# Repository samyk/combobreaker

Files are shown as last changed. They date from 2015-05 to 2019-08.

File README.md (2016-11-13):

# [C-C-C-C-Combo Breaker](http://samy.pl/combobreaker/)

**[Combo Breaker](http://samy.pl/combobreaker/)** is a motorized, battery powered, 3D printed, Arduino-based combination lock cracking device. It is portable, open source, 3D models provided, and exploits a new technique I've discovered for [cracking combination locks in 8 attempts or less](https://www.youtube.com/watch?v=09UgmwtL12c), but in an even more exciting, automated fashion.

By [@SamyKamkar](https://twitter.com/samykamkar)

#### Follow me on [Twitter](https://twitter.com/samykamkar) or [join my mailing list](http://samy.pl/list/) to hear about future projects and research.

**Live demonstration** and full details available in [the video](https://www.youtube.com/watch?v=YcpSvHpbHQ4):
<a href="https://www.youtube.com/watch?v=YcpSvHpbHQ4" target="_blank">KeySweeper</a>

-----

**Point of Contact:** [@SamyKamkar](https://twitter.com/samykamkar) // <http://samy.pl>

**Video demonstration / explanation:** [https://youtu.be/YcpSvHpbHQ4](https://youtu.be/YcpSvHpbHQ4)

**Released:** May 14, 2015

**Source code / 3D models:** [https://github.com/samyk/combobreaker](https://github.com/samyk/combobreaker)

**Unit Cost:** < $100

**Status:** Operational, open source, open hardware, declassified.

-----

# (U) Hardware

Combo Breaker (http://samy.pl/combobreaker/sIMG_2916.JPG)

### [Arduino Nano](http://amzn.to/1QLlf23)
**$12**: A [5V Arduino Nano](http://amzn.to/1QLlf23) microcontroller is used as the brains of the project.

### [Allegro A3967 / EasyDriver Stepper Driver](http://amzn.to/1A1Ovxl)
**$20**: I originally used an A3967-based [EasyDriver](http://amzn.to/1A1Ovxl) which can drive a stepper motor up to 30V at 750mA. This is what precisely controls the dial.

### or [Allegro A4988](http://amzn.to/1L3q7fK)
**$7**: Instead of the EasyDriver, I upgraded to a smaller, yet more powerful stepper driver that can go up to 1 amp (1000mA).

### [Stepper Motor](http://amzn.to/1FfLUQG)
**$30**: You can use a normal stepper motor for the "simpler" version of the Combo Breaker build, however if you're working on creating the more advanced version, you'll need a double-shaft stepper motor like I liste below.

### or [Double Shaft Stepper Motor](http://www.phidgets.com/products.php?product_id=3320)
**$16**: This double shaft stepper motor allows you to build the more advanced Combo Breaker while employing an optical rotary encoder on the back to detect the position of the stepper when the dial stops turning (which is part of the exploit employed).

### [HKT22 Optical Rotary Encoder](http://www.phidgets.com/products.php?product_id=3531)
**$25**: For use **only** with the double shaft stepper motor, this optical rotary encoder lets us know what position the shaft of the stepper motor is at and allows us to employ an exploit on Master combination locks where the stepper will get locked into certain grooves within the internal combination disc of the lock.

### [Analog Feedback Servo](https://www.adafruit.com/products/1404)
**$15**: This servo not only provides the torque we need to lift the shackle (90.26 oz*in), but has an additional wire providing analog feedback that we use to detect the state of the shackle and whether it has opened or not.

### [L7805 Voltage Regulators](http://amzn.to/1A28XOt)
**$6**: If you're using the analog feedback servo, you'll want to use an external voltage regulator to provide enough juice to the servo. While the Arduino is 5V and can drive the servo normally, it won't be able to pump out enough current for the servo when it starts hitting the shackle and could damage your Arduino.

### [500mAh 3S Lipo Battery](http://amzn.to/1PkRVlz)
**$20**: This 500mAh 3S (3-cell, 11.1V) battery gives enough juice to the stepper motor to be very effective, and at 500mAh can last between 30-120minutes straight before having to be recharged.

### [Lipo Charger](http://amzn.to/1A1Q2n7)
**$50**: This lipo charger is overkill if only used for this project, but is a good one that I use at home for a wide range of batteries and cells. You don't need this one, but if you want to recharge the battery, you'll need a charger that supports 3-cell LiPos.

### [Arctic Alumina Thermal Adehsive](http://amzn.to/1PkTakG)
**$8**: Not required, but this is the thermal **adhesive** I use to **permanently** attach the heatsink to the stepper motor driver. Normal thermal paste has very little adhesion and kept falling off, so I switched from thermal paste to this thermal adhesive.

### [Digital Calipers](http://amzn.to/1K8juex)
**$16**: If you don't already have digital calipers for precise measurements to measure the lock, for example, these are inexpensive and accurate.

### [Breadboard and Wires](http://amzn.to/1FfMb6e)
**$6**: If you don't already have a breadboard and wires, they will kind of help.

Combo Breaker (http://samy.pl/combobreaker/sIMG_2875.JPG)

Combo Breaker (http://samy.pl/combobreaker/sIMG_2920.JPG)

-----

# (U) Software

### Combo Breaker
Combo Breaker's source code can be obtained in entirety from my github: <https://github.com/samyk/combobreaker>

Combo Breaker 3D Print (http://samy.pl/combobreaker/model.jpg)

-----

# (U) 3D Models

I've included the 3D models on my github: <https://github.com/samyk/combobreaker>
 
Combo Breaker 3D Print (http://samy.pl/combobreaker/smodel.png)

Combo Breaker (http://samy.pl/combobreaker/sIMG_2919.JPG)

-----

# (U) Contact

**Point of Contact:** [@SamyKamkar](https://twitter.com/samykamkar)

You can see more of my projects at <http://samy.pl>.

#### Follow me on [Twitter](https://twitter.com/samykamkar) or [join my mailing list](http://samy.pl/list/) to hear about future projects and research.

Thanks!

------

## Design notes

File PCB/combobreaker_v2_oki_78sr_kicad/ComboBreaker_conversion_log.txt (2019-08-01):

#********** START OF renumber-sheet.ulp ULP Version 4.4.4 12-03-2017 :20:05:27 LOG **********#
#OldRef				SheetNumber	NewRef
ARDUINO				1	ARDUINO4989
ENCODER				1	ENCODER4989
OKI-78SR				1	OKI-78SR4989
SERVO				1	SERVO4989
STEPPER				1	STEPPER4989
#********** END OF renumber-sheet.ulp ULP Version 4.4.4 12-03-2017 :20:05:27 LOG **********#

#********** START OF fix_via_hack.ulp ULP Version 4.6.0 12-03-2017 :20:05:32 LOG **********#
PADFILL	PadCount=60		Net=GND				(X=8145.000000 Y=34052.000000)	LayerStart=1	LayerEnd=1
#********** END OF fix_via_hack.ulp ULP Version 4.6.0 12-03-2017 :20:05:32 LOG **********#

#********** START OF eagle6xx-sch-to-kicad-sch.ulp 1.9 12-03-2017 :20:06:57 LOG **********#
    Conversion completed with no Messages
#********** END OF eagle6xx-sch-to-kicad-sch.ulp 1.9 12-03-2017 :20:06:57 LOG **********#

#********** START OF exp-lbrs.ulp 6.6 12-03-2017 :20:11:32 LOG **********#
OK: Eagle lib export from SCH/PCB OK
    Conversion completed with no Messages
#********** END OF exp-lbrs.ulp 6.6 12-03-2017 :20:11:32 LOG **********#

#********** START OF eagle-lbr2kicad-1.0.ulp 2.7 12-03-2017 :20:11:44 LOG **********#
Missing Prefix Part =''				A4988BREAKOUT					ComboBreaker		M
Missing Prefix Part =''				OKI-78SRH					ComboBreaker		M
#********** END OF eagle-lbr2kicad-1.0.ulp 2.7 12-03-2017 :20:11:44 LOG **********#

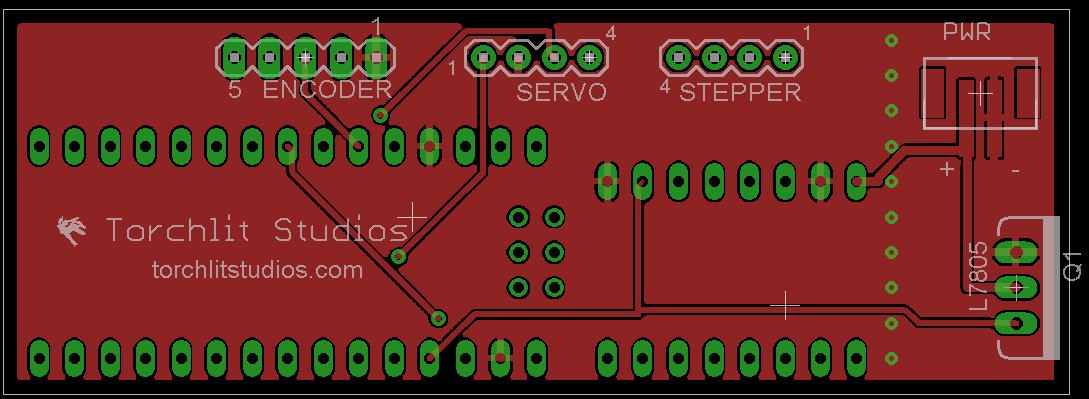
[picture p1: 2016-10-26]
Eagle Files/ComboBreaker_top.png

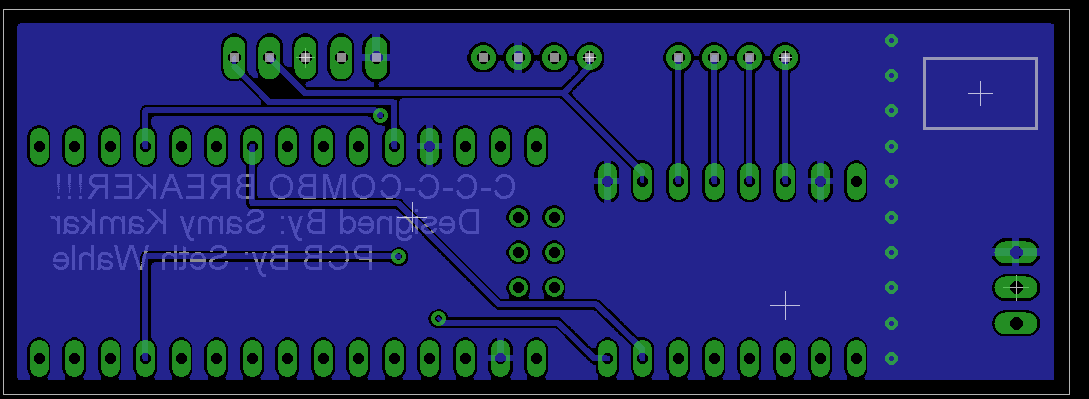
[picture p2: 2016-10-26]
Eagle Files/ComboBreaker_bottom.png

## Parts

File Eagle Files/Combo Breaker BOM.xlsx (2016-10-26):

JST-PH-2-SMT | https://www.sparkfun.com/products/8612
L7805CV | http://www.mouser.com/ProductDetail/STMicroelectronics/L7805CV/?qs=9NrABl3fj%2FqplZAHiYUxWg%3D%3D
STEP-STICK | http://www.ebay.com/itm/like/281574528914?lpid=82&chn=ps
Arduino Nano | http://www.newegg.com/Product/Product.aspx?Item=9SIA7BF2K19102&nm_mc=KNC-GoogleMKP-PC&gclsrc=aw.ds
Pin Headers | https://www.sparkfun.com/products/116

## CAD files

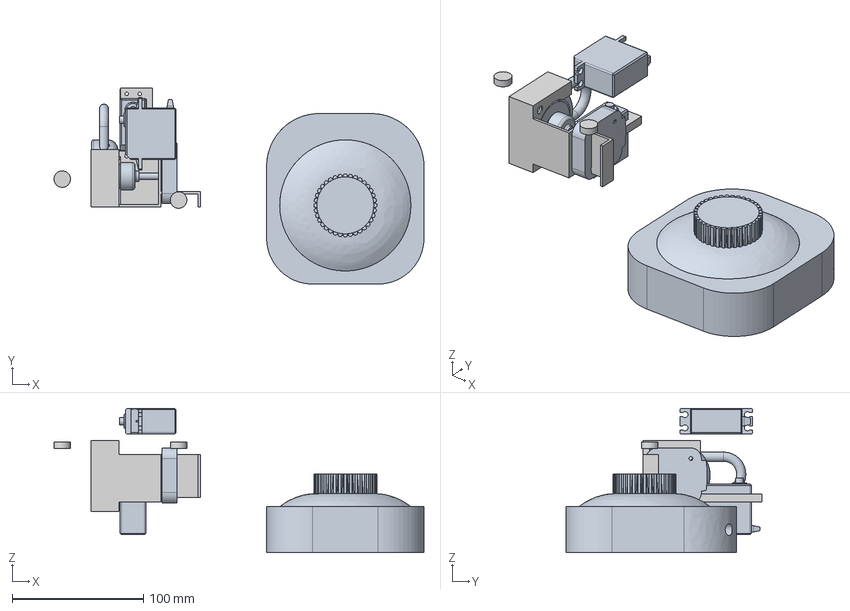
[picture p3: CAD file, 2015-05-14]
3dmodels/combo-breaker-chassis.igs
282.1 x 149.6 x 109.9 mm

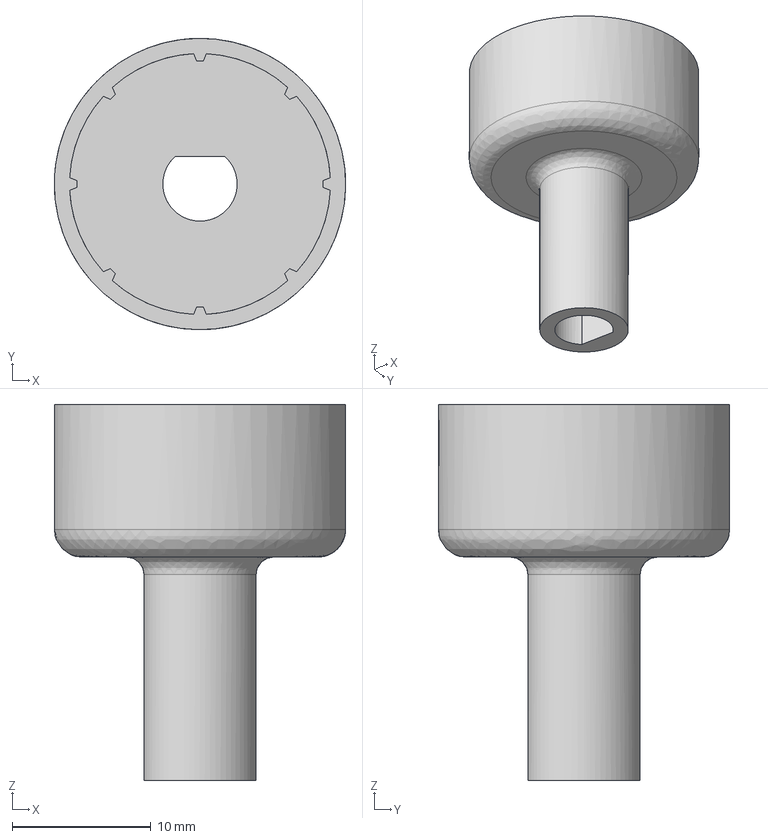
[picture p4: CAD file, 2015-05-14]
3dmodels/stepper-long-gripper.igs
21.0 x 21.0 x 27.1 mm

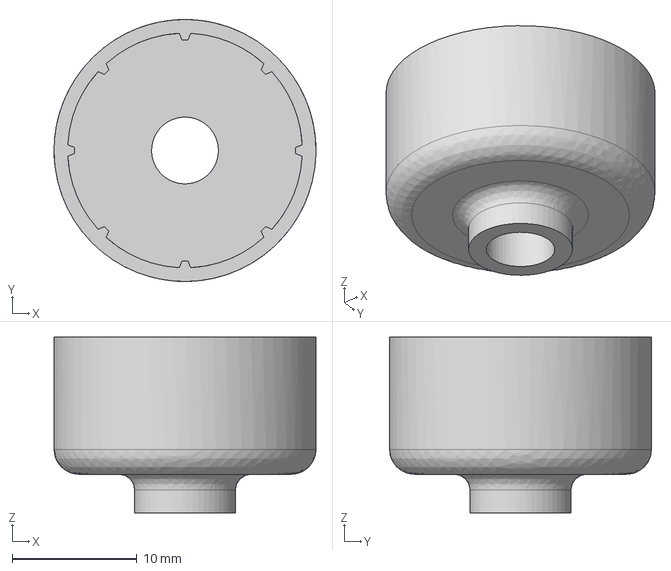
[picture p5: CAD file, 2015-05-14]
3dmodels/pancake-stepper-gripper.igs
21.0 x 21.0 x 14.1 mm

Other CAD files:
3dmodels/combo-breaker-chassis.f3d
3dmodels/pancake-stepper-gripper.f3d
STL Files/combo-breaker-chassis.stl
STL Files/pancake-stepper-gripper.stl
STL Files/stepper-long-gripper.stl

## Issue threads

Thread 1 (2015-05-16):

How Combo breaker work?

thanhmssl10, 2015-05-16:
Your project is so Awesomeeeeee!! :smile:
But i want to know how it work, i don't think it Brute force with only 30s :smile:

samyk, 2015-05-16:
These videos explain the reduction attack:
https://www.youtube.com/watch?v=09UgmwtL12c (online tool)
https://www.youtube.com/watch?v=qkolWO6pAL8 (actual vuln)

Scott216, 2015-05-18:
I just finished watching your videos.  You are the combo-lock whisperer :)

geek213, 2015-05-28:
building the advanced combo breaker - having the parts printed for me.
do i just need the combo-breaker-chassis code? (does that code it include  a dial-gripper?)
- or do i need to send the stepper-long-gripper code too?
thx

samyk, 2015-05-28:
You need to print a gripper that works for the stepper motor you chose (look at the length of the arm and whether the shaft shape is a D or O). You may need to adjust for tolerances in your print as well.

geek213, 2015-05-28:
the shaft is an "O"; diameter is ,195" and the length is .717".
would i print the stepper-long-gripper and cut to length?

chefterry76, 2016-12-28:
where is the code for the basic version tnx

Closed 2015-05-16.

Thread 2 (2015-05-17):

Fusion 360 file

Scott216, 2015-05-17:
Cool project.  I may build this with my kids.  I really like Fusion 360.  Can you make your Fusion 360 file public?

samyk, 2015-05-17:
I've just added two of the f3d (fusion 360 archive) files to the 3dmodels directory. You may need to alter the gripper for your stepper motor. Have fun!

Closed 2015-05-17.

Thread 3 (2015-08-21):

Wiring diagram

LottieBot, 2015-08-21:
Hi sammy its me lottie again (sorry for badgering you).But i want to bring up a inmportaint subject witch is the wiring diagram.If the combo breaker is fully open sourse then i would imagine that a wiring graph would be necessary.I and a lot of other folks out there aren't that aware about wiring or electronics.

thats all,sorry for pestering you

TheHoopla, 2016-03-30:
Bump on this btw

AidanMcCarthy, 2019-08-01:
This is all available in the new merge. Issue can be closed @samyk

samyk, 2019-08-01:
Thanks @AidanMcCarthy!

Closed 2019-08-01.

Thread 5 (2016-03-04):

wiring

begginer500, 2016-03-04:
Hi Samy,
I was just wondering if you could send me something that helps with the wiring on the combo breaker when you get a chance.
Thanks. :)

LottieBot, 2016-03-12:
hey dude i have actually been working on this project and made a prototype but im rebuilding it because it was crap, but im learning eagle cad and i will show you the wiring diagram when im finished sound funky?

begginer500, 2016-03-16:
Thanks I really appreciate it LottieBot. :)

LottieBot, 2016-03-16:
no prob bob, im going to get some more help on the adafruit fourms to clarify my design

TheHoopla, 2016-03-30:
Hey, did you ever get a wiring diagram working?

LottieBot, 2016-03-30:
yeah i made a pcb but i had to do some funky stuff to the schmatic so that it would produce a pcb in eagle cad @TheHoopla

TheHoopla, 2016-03-30:
Could I see your PCB? That would be amazing. I'm working on this and the wiring is killing me.

LottieBot, 2016-03-30:
i have sent it out to a pcb house but im not shure if the wiring is correct well if you can confirm that, it would be amazing if you actually test it. @TheHoopla

TheHoopla, 2016-03-30:
We're using pcbArtist so if it's in an .sch or .pcb that would be incredible.

LottieBot, 2016-03-30:
still unshure how to turn the nobby thinggy on the a4988 if you can help me out that would be awesome @TheHoopla

LottieBot, 2016-03-30:
@TheHoopla im using eaglecad

TheHoopla, 2016-03-30:
Do you have the file?

LottieBot, 2016-03-30:
yeah
@TheHoopla

TheHoopla, 2016-03-30:
Do you have the eagle file?

LottieBot, 2016-03-30:
im uploading it in a zip right now

LottieBot, 2016-03-30:
just the board

TheHoopla, 2016-03-30:
Awesome!

TheHoopla, 2016-03-30:
You're a life saver man

LottieBot, 2016-03-30:
yeah i know

LottieBot, 2016-03-30:
that feeling

LottieBot, 2016-03-30:
actually i will link it too my google drive

LottieBot, 2016-03-30:
not working

TheHoopla, 2016-03-30:
The file will be in your repo right? I'm just hitting refresh until I see it haha

TheHoopla, 2016-03-30:
Ok sounds good

LottieBot, 2016-03-30:
yeah im new to github but for right now i am using gdocs

LottieBot, 2016-03-30:
https://drive.google.com/open?id=0B4ow_apMkuGseGtSaFVCVzc3Ykk

TheHoopla, 2016-03-30:
Thank yoooou

LottieBot, 2016-03-30:
and i uploaded the sch aswell if you are intrested

TheHoopla, 2016-03-30:
Oh could you give access to jacobwilliamson@utexas.edu

LottieBot, 2016-03-30:
if you give them the link it should be good

LottieBot, 2016-03-30:
remember @TheHoopla the only thing that i can confirm works is the servo i do not know about the stepper or the encoder, my pcb is not here yet so im going based on theoretical predictions so dont get your hopes up yet

LottieBot, 2016-03-30:
but if you can help me solve how much the screw nob on the stepper driver has to be turned then we could wrap it up

TheHoopla, 2016-03-30:
Lab partner is asking for permission lol

TheHoopla, 2016-03-30:
And yeah we'll check all the connections, test it too, and tell you what we get

TheHoopla, 2016-03-30:
(Btw the google drive is definitely locked)

LottieBot, 2016-03-30:
sorry lemme change it

LottieBot, 2016-03-30:
https://drive.google.com/folderview?id=0B4ow_apMkuGseGtSaFVCVzc3Ykk&usp=sharing

LottieBot, 2016-03-30:
i think this one is shareable

LottieBot, 2016-03-30:
@TheHoopla also if you plan on using this as a project or for selling ask me first :3

LottieBot, 2016-03-30:
but if your using it for a project you dont have to ask me because we just talked so its cool :)

LottieBot, 2016-03-30:
@TheHoopla btw thanks for the connection testing i really appreciate the verification, it is making the project one step closer to completion

TheHoopla, 2016-03-30:
We're doing a variation of this for a class lab. We're doing it on a TM4C123 chip instead of the arduino. We'll tell you any and all info we get!

LottieBot, 2016-03-30:
@TheHoopla also my if you comment on my new video (https://www.youtube.com/watch?v=rgl9w4gDVLU ) there is another guy there in the comments eager to hear more from this project and we can discuss stuff there i guess?

LottieBot, 2016-03-30:
@TheHoopla oh sweet :P

LottieBot, 2016-03-30:
@TheHoopla please tell me how to twist the potentiometer on the stepper motor driver if you get the chance :3

LottieBot, 2016-04-11:
@TheHoopla found a problem with my pcb board when i soldered everything together so this weekend i am going to create the pcb by scratch :3

kthomas22, 2016-10-26:
What was the issue with the PCB, wiring issue or something else?

htmagic, 2017-01-14:
Bump! So is the PCB good now? What is the status on this? Thank you to all the folks that helped on this. I recently came across Samy's site and saw this. This will make for a cool magic trick I'm working on...

cnewlander, 2017-02-19:
I believe the PCB wiring is not correct for the L7805 voltage regulator.   The output PIN appears to be correct.  The INPUT and GND connections are reversed.      I blew through two Arduino Nano due to this.   Good times.

teamstarlet, 2017-02-19:
I found this issue a few weeks back. Looks like the package used in Eagle was for a L7905 which has the I/G pins reversed.

I'm just working on revising this along with some other aspects of the board and will upload once it's finished.

cnewlander, 2017-02-19:
I would recommend removing the vias bordering the N4$ and N$11 nets.    Depending on the tolerance of manufacturing the vias especially around N$4 net are awful close and I fear shorting a LiPo battery.  :)  There are plenty of vias to connect the top and bottom GNDs.

htmagic, 2017-02-20:
OK, so flip the voltage regulator underneath and solder it under the PCB. Then the input and Gnd will be reversed and correct.
Or you could flip the L7805 around and have the heat sink towards the center of the board.
Have the Eagle files been corrected?
I'm not sure how to reprogram the Eagle files.
And is there a schematic somewhere? I don't believe i ever saw one...

Thank you for your help.

----- Original Message -----

From: "cnewlander" <notifications@github.com>
To: "samyk/combobreaker" <combobreaker@noreply.github.com>
Cc: "htmagic" <htmagic@comcast.net>, "Comment" <comment@noreply.github.com>
Sent: Sunday, February 19, 2017 5:09:07 PM
Subject: Re: [samyk/combobreaker] wiring (#5)

I believe the PCB wiring is not correct for the L7805 voltage regulator. The output PIN appears to be correct. The INPUT and GND connections are reversed. I blew through two Arduino Nano due to this. Good times.

—
You are receiving this because you commented.
Reply to this email directly, view it on GitHub , or mute the thread .
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
teamstarlet, 2017-03-06:
I believe I've found the issue with the stepper code. The servo and stepper are doing their job now. PCB should be finished shortly.

@htmagic `void `in this instance defines a function, it's not the same as disabling a line of code by  commenting it out with `//`

htmagic, 2017-03-06:
So what was the issue so I can learn this as well?

----- Original Message -----

From: "Aidan McCarthy" <notifications@github.com>
To: "samyk/combobreaker" <combobreaker@noreply.github.com>
Cc: "htmagic" <htmagic@comcast.net>, "Mention" <mention@noreply.github.com>
Sent: Monday, March 6, 2017 10:11:33 AM
Subject: Re: [samyk/combobreaker] wiring (#5)

I believe I've found the issue with the stepper code. The servo and stepper are doing their job now. PCB should be finished shortly.

@htmagic void in this instance defines a function, it's not the same as disabling a line of code by commenting it out with //

—
You are receiving this because you were mentioned.
Reply to this email directly, view it on GitHub , or mute the thread .

teamstarlet, 2017-03-06:
Once I've got everything confirmed and tested completely I'll list all the changes.

jkwann, 2017-03-21:
@teamstarlet Hi, I am trying to build this combobreaker as well. I am also running into issues with the stepper motor (not stepping correctly and making a lot of noise). If you got a solution, can you kindly provide the modified code? Thanks.

teamstarlet, 2017-03-21:
@jkwann I did discover after a lot of trial and error that the issue with the stepper was related to the `#define MIN_DELAY (1600 / MICROSTEPS) // was 200` on line 56.

I've been experimenting with numbers but am waiting to get my proto board back from the printer before testing further.

You should be able to set it to 400 if recall, and it should work.

cnewlander, 2017-03-21:
htmagic, the component package is specified incorrectly for the L7805 voltage regulator.  The BRD and SCH files have not been updated in two years.  Do not use the current BRD file for PCB production.   It won't work.

jkwann, 2017-03-27:
@teamstarlet Hey, thanks for your reply, I got the motor running! The issue I am having right now is that the device is using the brute force method instead of the optimal algorithm which takes forever. Could you please point me to the right direction? Thanks. @samyk

teamstarlet, 2017-03-27:
Great!

I'm just waiting on my prototype boards to come in but once they're here I will be able to start working on the code.

cnewlander, 2017-03-27:
Can someone post the wiring for stepper,  servo, encoder.  Or post where the  information can be found?

On Mar 27, 2017, at 6:19 PM, Aidan McCarthy <notifications@github.com<mailto:notifications@github.com>> wrote:

Great!

I'm just waiting on my prototype boards to come in but once they're here I will be able to start working on the code.

—
You are receiving this because you commented.
Reply to this email directly, view it on GitHub<https://github.com/samyk/combobreaker/issues/5#issuecomment-289603325>, or mute the thread<https://github.com/notifications/unsubscribe-auth/AYPC6jMFoMAWM22jZ-ZaI5MB8tIQJz-Sks5rqDYAgaJpZM4HpDou>.

teamstarlet, 2017-03-27:
You can check out my latest PCB [here](https://github.com/teamstarlet/combobreaker/tree/master/PCB/combobreaker_v2_oki_78sr_eagle)

It has all the info you're looking for :)

cnewlander, 2017-03-27:
Thanks.

On Mar 27, 2017, at 6:35 PM, Aidan McCarthy <notifications@github.com<mailto:notifications@github.com>> wrote:

You can check out my latest PCB here<https://github.com/teamstarlet/combobreaker/tree/master/PCB/combobreaker_v2_oki_78sr_eagle>

It has all the info you're looking for :)

—
You are receiving this because you commented.
Reply to this email directly, view it on GitHub<https://github.com/samyk/combobreaker/issues/5#issuecomment-289606296>, or mute the thread<https://github.com/notifications/unsubscribe-auth/AYPC6snQvI001h3xIuwpnao3tBk6fWI_ks5rqDl-gaJpZM4HpDou>.

teamstarlet, 2017-05-08:
I've tested the code and resolved the errors that were causing the stepper to not step correctly. You can check out the code on [my branch of ComboBreaker](https://github.com/teamstarlet/combobreaker/blob/master/combobreaker.ino)

There is one grounding issue with the PCB which I'll resolve shortly, other than that [my version of the PCB](https://github.com/teamstarlet/combobreaker/tree/master/PCB/combobreaker_v2_oki_78sr_eagle) has been fully tested.

adamaero, 2017-09-09:
Here is the difference between teamstarlet's code and the original:
https://www.diffchecker.com/el1w92Dn

AidanMcCarthy, 2019-08-01:
@samyk Issue can probs be closed now?

samyk, 2019-08-01:
Sure, why not

Closed 2019-08-01.

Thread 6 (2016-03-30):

Prototype design coming soon

LottieBot, 2016-03-30:
Hello everybody i have been talking to some people and i am hoping to get a prototype up and running before or during summer break i have made a pcb and i am getting the schmatic tested out and verified i will be revising the pcb design if needed.expect anoter update in a week or two and if it is working then i will be making s tutorial video and be open to pre made requests. ;3
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

kennyevanadams, 2016-11-17:
How did this pcb go?

LottieBot, 2016-11-18:
I ordered them a while ago, didnt work (probbley because i didnt autoroute) but i have another design ready to go.Now i only need to order them again

kennyevanadams, 2016-11-18:
thinking about ordering a custom pcb. Would you be willing to share your pcb design with me and if i make a youtube video i would give you credit of course.

LottieBot, 2016-11-18:
Oh yeah of couse i also was planning on doing a youtube video aswell.my computer recently had hard drive malfunctions so i lost my pcb.But no worries i have a backup and ill get it out today or tomorrow (im using fritzing btw).

kennyevanadams, 2016-11-18:
cool thanks so much just post it here or email me if u need my email just let me know

kennyevanadams, 2016-11-24:
Did u find the file?

LottieBot, 2016-11-24:
Yeah im on vacation i over estimated how long i need to take est 1 week

LottiebotTurbo, 2016-12-14:
in the mean time i have a schemtic i used http://imgur.com/a/Ci0Kp from oseth (this is the one i used) for my board.However i did make a revision 2 to the board using fritzing but lost it due to my HDD failing.Im busy with finals and other projects currently so if you make a board show me your results because i would like to compare it to my revisions. sorry about the long delay by the way.If i have time i might work on another revision but dont count on it.

AidanMcCarthy, 2019-08-01:
@samyk This issue can probably also be closed.

samyk, 2019-08-01:
Thanks @AidanMcCarthy!

Closed 2019-08-01.

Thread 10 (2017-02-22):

Where is the encoder.h file that is <included> in the combobreaker.ino sketch file?

cnewlander, 2017-02-22:
The combobreaker.ino will not compile with either arduino 1.6.13 or 1.8 because the header file encoder.h is missing.   Where can this file be sourced?   Or what needs to be configured to get this sketch to compile?

teamstarlet, 2017-02-22:
Try here:
https://www.pjrc.com/teensy/td_libs_Encoder.html

Not sure if this is the same one that @samyk used?

cnewlander, 2017-03-01:
Thanks, but if you aren't sure your suggestion is not helpful and only adds confusion.   :)

samyk, 2017-03-04:
@teamstarlet is correct

cnewlander, 2017-03-05:
Thanks @teamstarlet , @samylk

The above library is included with Arduino 1.6.13  To install it:

Arduion IDE -> Sketch -> Include Library -> Manage Libraries -> enter "encoder" in the "filter your search..." textbox.  Then select the Encoder by Paul Stoffregen then select the install button.

 installed version 1.4.1 and the code compiles.

sl33p3rc3ll, 2017-03-16:
Thanks to all!

Closed 2017-03-04.

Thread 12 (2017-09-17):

L7805 5V Regulator Connection Concern

adamaero, 2017-09-17:
The datasheet for the L7805 says that Pin 2 is ground--then why is it connected to the +5V of the power?
(Smoke started fuming, and wires burned when prototyped on the breadboard.)
After switching to a power supply (not a battery), the overload feature kicked in since it was drawing more than an amp! I'll start from scratch and re-wire, but I just want to understand why Pin 2 is not grounded.

https://www.sparkfun.com/datasheets/Components/LM7805.pdf

teamstarlet, 2017-09-17:
This has already been corrected. Check out the board that I designed in my
form of the project.

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

adamaero, 2017-09-18:
I will look at your schematic, thanks. Although the Eagle layout (not schematic) is the same for the L7805:
**https://github.com/teamstarlet/combobreaker/blob/master/Eagle%20Files/ComboBreaker_top.png**
same connections as
https://github.com/samyk/combobreaker/blob/master/Eagle%20Files/ComboBreaker_top.png

teamstarlet, 2017-09-18:
https://github.com/teamstarlet/combobreaker/tree/master/PCB

There is the corrected original PCB in there, as well as a much improved (but still needing some work) v2 Eagle PCB that uses a much more efficient OKI78SR for the 5V conversion.

***There's an issue with the grounding of the input power connector which needs to be fixed so I wouldn't send this directly off to be printed unless you want to solder some extra wires!***

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

AidanMcCarthy, 2019-08-01:
@samyk This issue can be closed now!

samyk, 2019-08-01:
Thanks @AidanMcCarthy!

adamaero, 2019-08-02:
(I think I just powered the Arduino incorrectly by using an external power supply and the Arduino's USB.)

Closed 2019-08-01.

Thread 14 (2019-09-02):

Breadboard wiring

Omegaleg, 2019-09-02:
Hey Samyk can you post the breadboard schematic for the simpler combo breaker you showed in your video?

mlemasters2002, 2019-09-09:
there have been many to ask for this in the past.  I know there has been some work on developing the PCB, that might help to understand.  We are about to start this project as well, just got the parts, but now comes the more difficult part.

Omegaleg, 2019-09-10:
Good luck on building, can you send me a picture of the wiring once you are done. That would be really help me out.

mlemasters2002, 2019-09-10:
I will share all I can, I have been looking at the wiring schematic and will likely start working on it in the next few weeks.  There was once a branch on this where folks where building a PCB, but that seems to be cleaned up now.  If you start and have success let everyone know.

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

AidanMcCarthy, 2019-09-10:
@mlemasters2002 @Omegaleg The branch with the PCB that I redesigned has been merged into the master branch under pull #13 .

Make sure to use the files under [https://github.com/samyk/combobreaker/tree/master/PCB/combobreaker_v2_oki_78sr_eagle](url)

You may well run into issues with the code once you've got the hardware setup. I managed to get it working at a very basic level but it seemed to only be bruteforcing and not using the algorithm. The stepper also didn't seem to have quite enough power to turn the dial if it was at all sticky or stiff.

mlemasters2002, 2019-09-10:
Thank you Aidan, have you heard of anyone getting this working yet?  As a brute force tool, have affective has it been?

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

AidanMcCarthy, 2019-09-10:
The best I've seen is [this one built by NYC CNC](https://www.youtube.com/watch?v=tteG2hQaDeg). I'm not aware of anyone that's successfully used this one to crack a lock.

Omegaleg, 2019-09-11:
@AidanMcCarthy so I followed the wiring diagram I found on Imgur https://imgur.com/a/Ci0Kp and got the hardware set up. I tried using your basic code but it kept saying saying: "stray @ in program". I tried deleting the @ but it still does not work, Im still a beginner and only have a basic knowledge code. Can you help me with the code, Im thinking of making this for my science project.

mlemasters2002, 2019-09-12:
We Will likely start the build this weekend, can you send a photo of your breadboard as well, if we notice anything we will come back and post as well.

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

mlemasters2002, 2019-09-14:
This wiring diagram looks a bit different from the diagram in the official project, did you have any luck getting it to work?

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

Omegaleg, 2019-09-16:
I finished the wiring, however the basic code doesn't work so Im still trying to figure out why.

mlemasters2002, 2019-09-17:
We have it mostly wired now, will be working on it again hopefully tomorrow night.  Did you have any luck so far in getting the stepper and server running?

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

Omegaleg, 2019-09-18:
Nope still working on code.

mlemasters2002, 2019-09-18:
Tonight we had some limited success, we believe all the wiring is correct as in the stepper is turning both right and left and the servo is lifting on the shackle.  However the dial receiver is too lose and we will have to do a slight redesign.  Also, I think we lowered the stepper power a bit too low.  The shackle are also needs to be extended, before we can really test.  I have no idea yet if the optical encoder is working yet.  I am looking to putting on the display to see if any errors occur.

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

Omegaleg, 2019-09-23:
So has anyone got it to work yet?

mlemasters2002, 2019-09-23:
Have to remodel some parts to really let it run.  Everything seems to be working but have not yet gotten it to unlock as the reviewer is slipping on the lock.  How about you, how far have you gotten?

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

Omegaleg, 2019-09-23:
I have wired everything onto the breadboard, but the simple code @AidanMcCarthy gave me still does not work.

mlemasters2002, 2019-09-24:
What code is it, is it different from that in the project.  Do you have control of the servo and the stepper?

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

mlemasters2002, 2019-09-24:
If you can send me the IMO, I will see if I can get it to work.  Does it compile?

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

mlemasters2002, 2019-09-24:
Does anyone have the brute force code that Samy mentions.  I don’t see a flag to set to brute force in the code.  I have the same experience with the stepper, the alignment  is not the best in the printed part.  If we get it working properly we will re-design the fram and share it out with everyone.  Aiden did you get your PCB working, can it be purchased?

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

AidanMcCarthy, 2019-09-24:
@mlemasters2002 DM me on Twitter at @Aidan_McCarthy

Omegaleg, 2019-09-25:
This is the code https://github.com/samyk/combobreaker/pull/13/commits/6d1320a91a40cb2a7e5487d147e57cca7abb74ca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

Omegaleg, 2019-09-30:
So anyone got the code to work yet?

mlemasters2002, 2019-09-30:
I didn’t get much done this weekend, will have to start up again this week.  I am hoping to have a new test by mid week.

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

AidanMcCarthy, 2019-09-30:
While chatting with @mlemasters2002 last week I ran some tests as well and got this working on a basic level.

https://github.com/AidanMcCarthy/combobreaker/commit/20867e955b5b0feb889a8362496fe3feb1a4cf06

mlemasters2002, 2019-09-30:
I noticed a new thing during the brut force, I need to record it and send it out.

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

mlemasters2002, 2019-10-01:
I am not sure if my last e-mail attached, I just sent Aidan the video via twitter.  Here is what I did, I am about to finish the Proto board as well, only a few more wires to go.

I could not upload to the project, here is the video.  I have modified my make shift hook arm.  Also, I have eighth step enable, I modified the code to fully put it back in,  I am not sure if the encoder is working, I wonder if there is a way to test if it is actually doing something. Notice at the end of the video what it is doing, does this seem right?  the receiver is slipping at the moment so it is all messed during that part of the cycle.

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

mlemasters2002, 2019-10-01:
Here are the edits I am working on, this is not fully tested yet, but I will test tonight.

https://github.com/mlemasters2002/combobreaker/blob/master/Combobreaker_Revised_10-01-2019.ino

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

mlemasters2002, 2019-10-05:
Should get some testing in this weekend on this, has anyone had any luck.  Aiden the new design is looking good. We will share out the new dial receiver this weekend.

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

mlemasters2002, 2019-10-05:
So I am a GitHub idiot, but I started a new branch because I have not had time to really play around yet.  I uploaded the dial receiver as a f3d file so you can play with it.  Aidan can you share the new chassis files, would like to see if we can add a version for the servo.
https://github.com/mlemasters2002/combobreaker/blob/master/MLCCC%20V3.1%20v2.f3d

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

Omegaleg, 2019-10-07:
Im still having trouble with the @AidanMcCarthy's code, here is the error message I am getting. And yes I did name the program danny devito.

danny_devito:1:1: error: stray '@' in program
 @@ -45,16 +45,15 @@
 ^
danny_devito:1:2: error: stray '@' in program
 @@ -45,16 +45,15 @@
  ^
danny_devito:1:18: error: stray '@' in program
 @@ -45,16 +45,15 @@
                  ^
danny_devito:1:19: error: stray '@' in program
 @@ -45,16 +45,15 @@
                   ^
danny_devito:21:1: error: stray '@' in program
 @@ -360,8 +359,9 @@ void step(int steps)
 ^
danny_devito:21:2: error: stray '@' in program
 @@ -360,8 +359,9 @@ void step(int steps)
  ^
danny_devito:21:18: error: stray '@' in program
 @@ -360,8 +359,9 @@ void step(int steps)
                  ^
danny_devito:21:19: error: stray '@' in program
 @@ -360,8 +359,9 @@ void step(int steps)
                   ^
danny_devito:1:4: error: expected unqualified-id before '-' token
 @@ -45,16 +45,15 @@
    ^
danny_devito:22:19: error: 'i' does not name a type
   for (int i = 0; i < steps * MICROSTEPS; i++)
                   ^
danny_devito:22:43: error: 'i' does not name a type
   for (int i = 0; i < steps * MICROSTEPS; i++)
                                           ^
exit status 1
stray '@' in program

mlemasters2002, 2019-10-08:
This is happening during compile? Have you tried the newest code yet?

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

Omegaleg, 2019-10-08:
Yes this is what is happening during compile.

Omegaleg, 2019-10-08:
Also where is the new basic code?

mlemasters2002, 2019-10-08:
Aidan uploaded yesterday or the day before on his branch.  I have not seen that compile error.

Sent from my iPhone

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

Omegaleg, 2019-10-09:
So where can I find it?

mlemasters2002, 2019-10-09:
https://github.com/AidanMcCarthy/combobreaker

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

Omegaleg, 2019-10-09:
Actually I worded it wrong. What I meant by basic code was the code for just the stepper motor. I wanted to make the simple version of the combo breaker.

mlemasters2002, 2019-10-09:
I have not seen code for the simple version.  The code that we are currently using is only doing brute force, which is the same as the simple version.  Currently we are working through some accuracy issues, the code is for the most part now actuating as expected.

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

Omegaleg, 2019-10-09:
so I could use the code you gave me without any modifications.

mlemasters2002, 2019-10-09:
The code is now doing what is expect, but we are seeing drift in the numbers, enough that ti would not work after about the 12th combination tried.  As a proof of concept I think it shows it is possible, but need to do some adjusting.  There is one difference from what I am doing and what Aidan is doing.  I am using micro stepping on the step stick and Aidan is doing it as speed.  I don’t know if one is better than the other, I did it because I was researching the step stick and found how to activate, now that it is all done, I figure I might as well keep it.  I will say all notion of skipping has been eliminated since I have activated micro stepping on the hardware side.

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

Omegaleg, 2019-10-09:
Well good luck to you guys and I hope you find the solution. The reason why i made this thread was to see if anyone could give me a detailed guide on how to make the simple combo breaker.

mlemasters2002, 2019-10-09:
I have looked for it as well, but have not found it, I don’t think it was ever published.

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

mlemasters2002, 2019-10-09:
If you have the simple code, send a link I can take a look.

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

Omegaleg, 2019-10-09:
Here is the simple code https://github.com/samyk/combobreaker/commit/6d1320a91a40cb2a7e5487d147e57cca7abb74ca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

@AidanMcCarthy updated it but Im still having the same issues.

mlemasters2002, 2019-10-10:
This is the code from 2017, but I just downloaded and it compiled fine on my computer.  This still has the optical encoder in the code which does not seem to be part of the simple build based on Sam’s original videos.  Do you have the optical encoder?

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

Omegaleg, 2019-10-10:
No how do I get rid of the optical encoder part. I just need the code for the stepper motor.

Omegaleg, 2019-10-16:
So did anyone find the basic code just for the motor driver?

AidanMcCarthy, 2019-10-16:
@Omegaleg The code doesn't exist. You would have to work on it yourself.

It's not too hard but you need some coding knowledge. This is very much a work-in-progress and not a fully tested solution that's ready for someone to click and be up and running.

Closed 2019-10-30.

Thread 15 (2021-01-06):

Reduction attack vs. combobreaker

jackattack21, 2021-01-06:
Not totally tracking the connection between this and the reduction attack. Not seeing anything in the duino code about finding resistance on the dial and identifying pins.

Is this a brute force attack of all combinations, just excluding combos that are geometrically impossible based on the tolerances of the locking mechanisms?

How many total possible combinations are tried?

Do you know anyone whose expanded on this and has servos and analog feedbacks doing the full reduction attack?

winstonriley4, 2021-02-21:
I know this GitHub is now quite old, but it seems like some folks are currently working on creating their own device.  I am currently doing this, so maybe there are folks wanting/willing to collaborate.

I too have been pouring over the code from this GitHub.  I only see the brute force attack in the code and a little working towards the reduction attack.  I watched Samy's videos (good stuff there) and have been able to break several locks using the technique shown.  So today I wrote code to figure out the possible codes from hardcoded numbers of the two lock position numbers, the resistive number, and the wider gap from the two 3rd combo numbers.  So this basically does what Samy's website does.

My current thinking and insights:
What I am now working on is how to find given numbers listed above.  At this point I am not convinced that the device as constructed from this thread is able to find any of the numbers.  I also noted that the code in the combobreaker.ino file is attempting to determine the 2 lock numbers between 0 and 10.  It does not involve the encoder which would be required to find these two numbers.  Also, can this device sense the resistive number using the stepper motor and the encoder?

Can anyone tell me if they have discovered how to find the input numbers, or even if it is not possible to do so  with this device.

I have also modified the project to include a LCD screen in the hopes of displaying the found combo numbers.  My stl files have been created to include a LCD and a power switch and button to start the cracking routines.  If I successfully create the ComboCracker then I will post my code and stl files.

Thanks for any thoughts on all this.

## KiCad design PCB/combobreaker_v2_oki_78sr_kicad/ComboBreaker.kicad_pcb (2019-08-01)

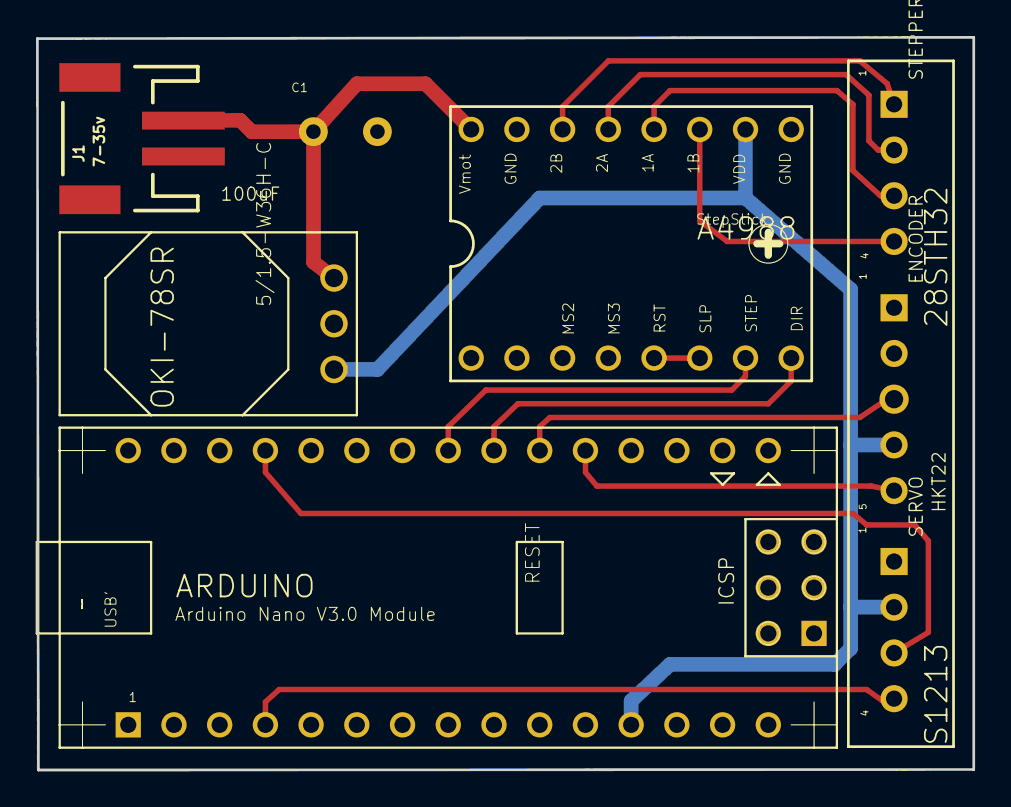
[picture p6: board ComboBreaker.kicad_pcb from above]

Board: 2 copper layers, 52.0 x 40.7 mm, 8 parts (0 on the bottom side), 14 nets.

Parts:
A4988: StepStick; A4988BREAKOUT
ARDUINO: Arduino Nano V3.0 Module; ARDUINO_NANO
C1: 100uF; E3,5-8
ENCODER: HKT22; MA05-1
J1: 7-35v; JST-2-SMD
OKI-78SR: 5/1.5-W36H-C; OKI-78SRH
SERVO: S1213; MA04-1
STEPPER: 28STH32; MA04-1

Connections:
1A_BLK: A4988.1B, STEPPER.4
1B_GRN: A4988.1A, STEPPER.3
2A_RED: A4988.2A, STEPPER.2
2B_BLU: A4988.2B, STEPPER.1
+5V: A4988.VDD, ARDUINO.12, ENCODER.4, OKI-78SR.3, SERVO.2
D2_CH_A_WHITE: ARDUINO.20, ENCODER.5
D3_CH_B_BROWN: ARDUINO.21, ENCODER.3
D9_SERVO: ARDUINO.27, SERVO.3
FEEDBACK: ARDUINO.4, SERVO.4
GND: A4988.GND, ARDUINO.14, ARDUINO.19, C1.-, ENCODER.1, J1.1, OKI-78SR.2, SERVO.1
unnamed: A4988.RST, A4988.SLP
unnamed: A4988.DIR, ARDUINO.22
unnamed: A4988.STEP, ARDUINO.23
VCC: A4988.VMOT, C1.+, J1.2, OKI-78SR.1

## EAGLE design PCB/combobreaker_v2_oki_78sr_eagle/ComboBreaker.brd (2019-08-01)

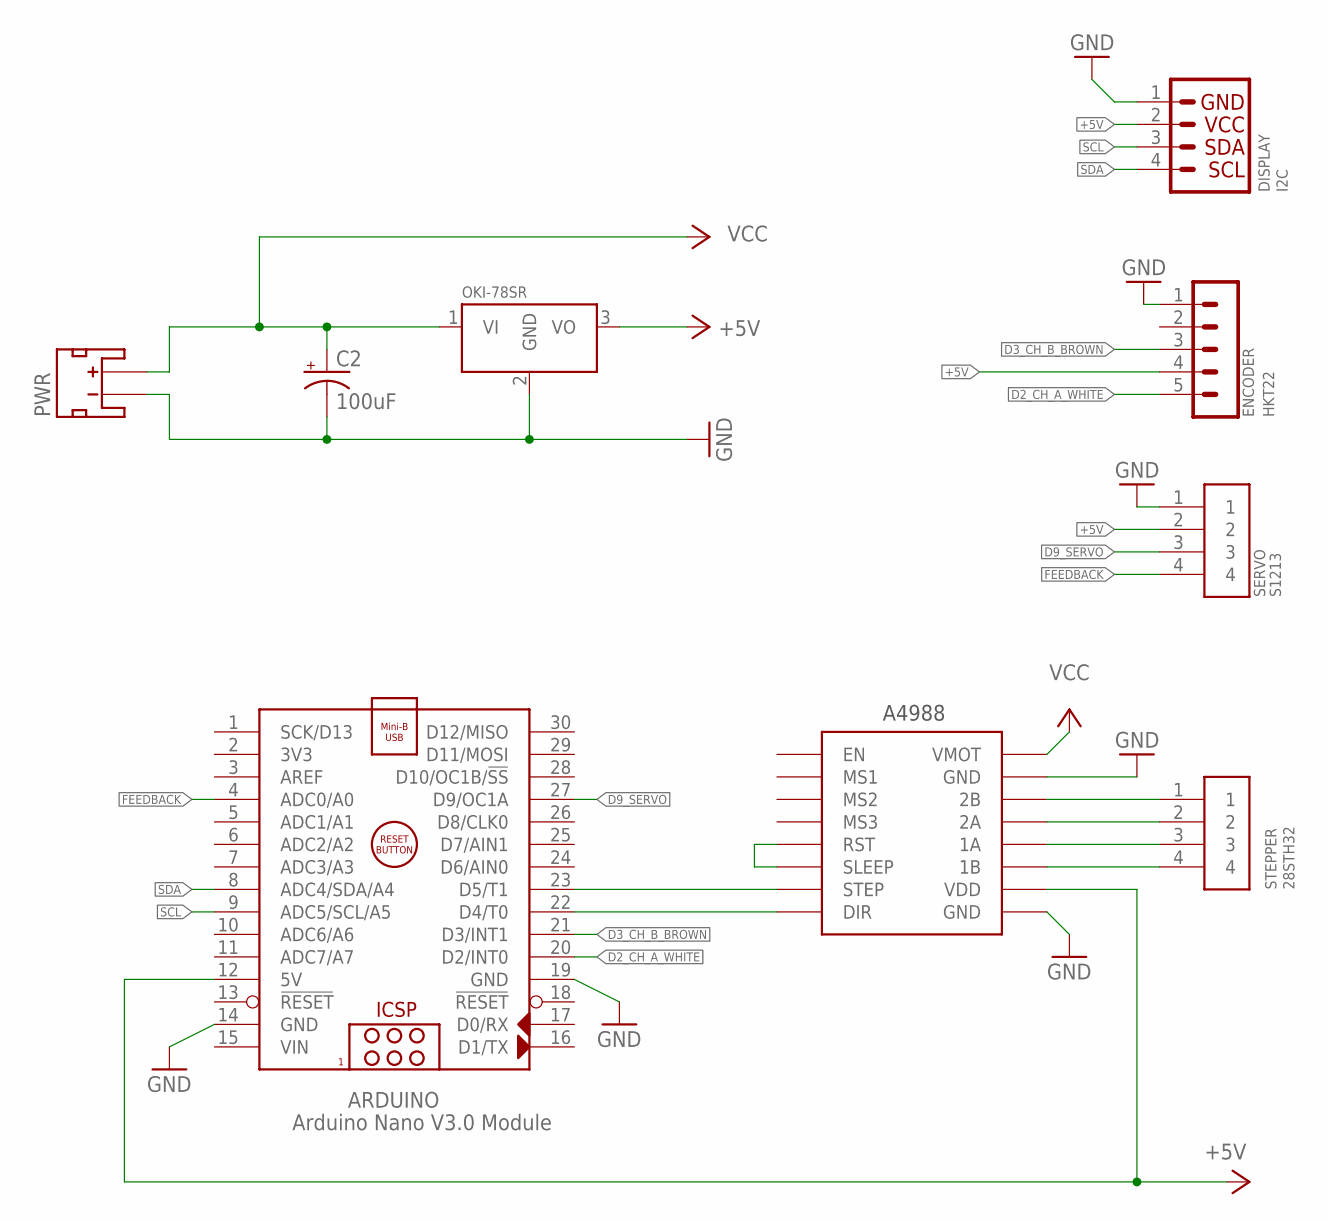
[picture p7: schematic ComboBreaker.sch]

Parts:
A4988: StepStick; A4988BREAKOUT
ARDUINO: Arduino Nano V3.0 Module; ARDUINO_NANO
C2: 100uF; E3,5-8
DISPLAY: I2C; 1X04
ENCODER: HKT22; CON-LSTB_MA05-1
OKI-78SR: 5/1.5-W36H-C; OKI-78SRH
PWR: 7-35v; JST-2-SMD
SERVO: S1213; ADAFRUIT_1X04-BIG
STEPPER: 28STH32; ADAFRUIT_1X04-BIG

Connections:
1A_GRN: A4988.1A, STEPPER.3
1B_BLK: A4988.1B, STEPPER.4
2A_RED: A4988.2A, STEPPER.2
2B_BLU: A4988.2B, STEPPER.1
+5V: A4988.VDD, ARDUINO.12 (5V), DISPLAY.2, ENCODER.4, OKI-78SR.3 (VO), SERVO.2
D2_CH_A_WHITE: ARDUINO.20 (D2/INT0), ENCODER.5
D3_CH_B_BROWN: ARDUINO.21 (D3/INT1), ENCODER.3
D9_SERVO: ARDUINO.27 (D9/OC1A), SERVO.3
FEEDBACK: ARDUINO.4 (ADC0/A0), SERVO.4
GND: A4988.GND, A4988.GND@0 (GND), ARDUINO.14 (GND), ARDUINO.19 (GND), C2.-, DISPLAY.1, ENCODER.1, OKI-78SR.2 (GND), PWR.GND (-), SERVO.1
unnamed: A4988.RST, A4988.SLP (SLEEP)
unnamed: A4988.DIR, ARDUINO.22 (D4/T0)
unnamed: A4988.STEP, ARDUINO.23 (D5/T1)
SCL: ARDUINO.9 (ADC5/SCL/A5), DISPLAY.3
SDA: ARDUINO.8 (ADC4/SDA/A4), DISPLAY.4
VCC: A4988.VMOT, C2.+, OKI-78SR.1 (VI), PWR.2 (+)
VIN: ARDUINO.15 (VIN)

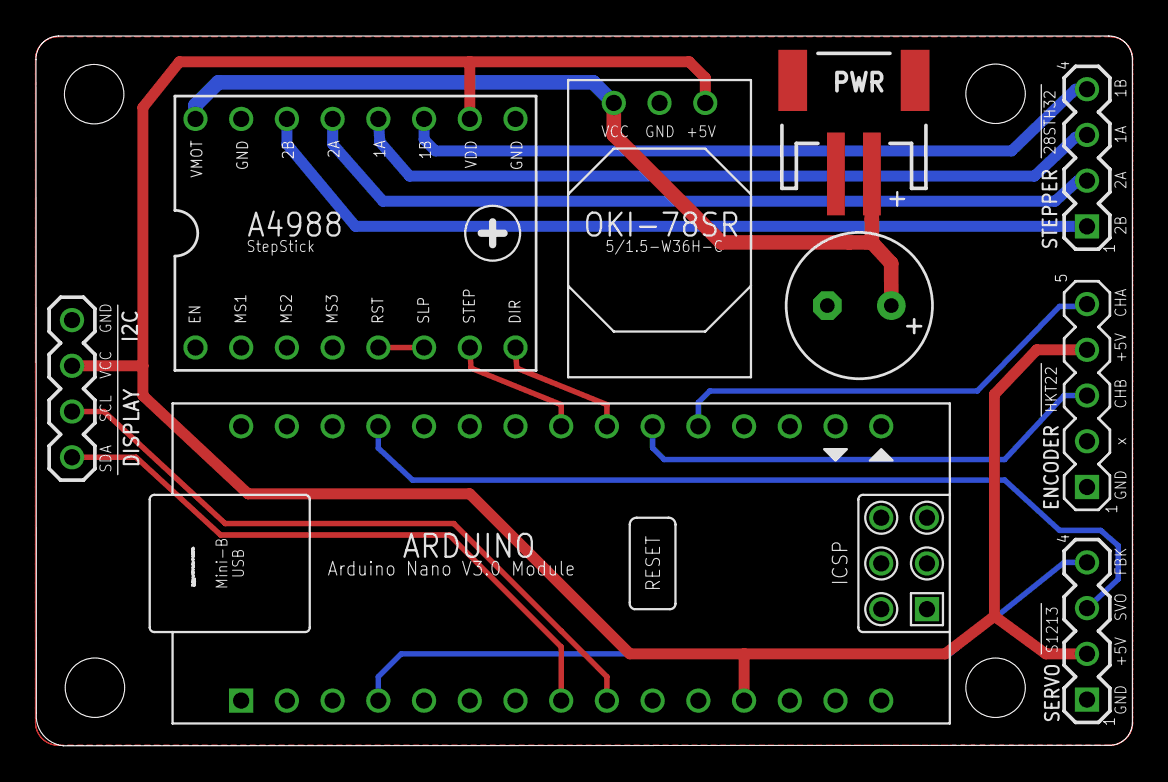
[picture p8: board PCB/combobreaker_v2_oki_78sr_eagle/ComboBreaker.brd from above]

Board: 2 copper layers, 60.9 x 39.4 mm, 15 parts (1 on the bottom side), 16 nets.

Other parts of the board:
U$1, U$2, U$3, U$4: STAND-OFF
U$5: AM
U$6: MASTERLOCK2

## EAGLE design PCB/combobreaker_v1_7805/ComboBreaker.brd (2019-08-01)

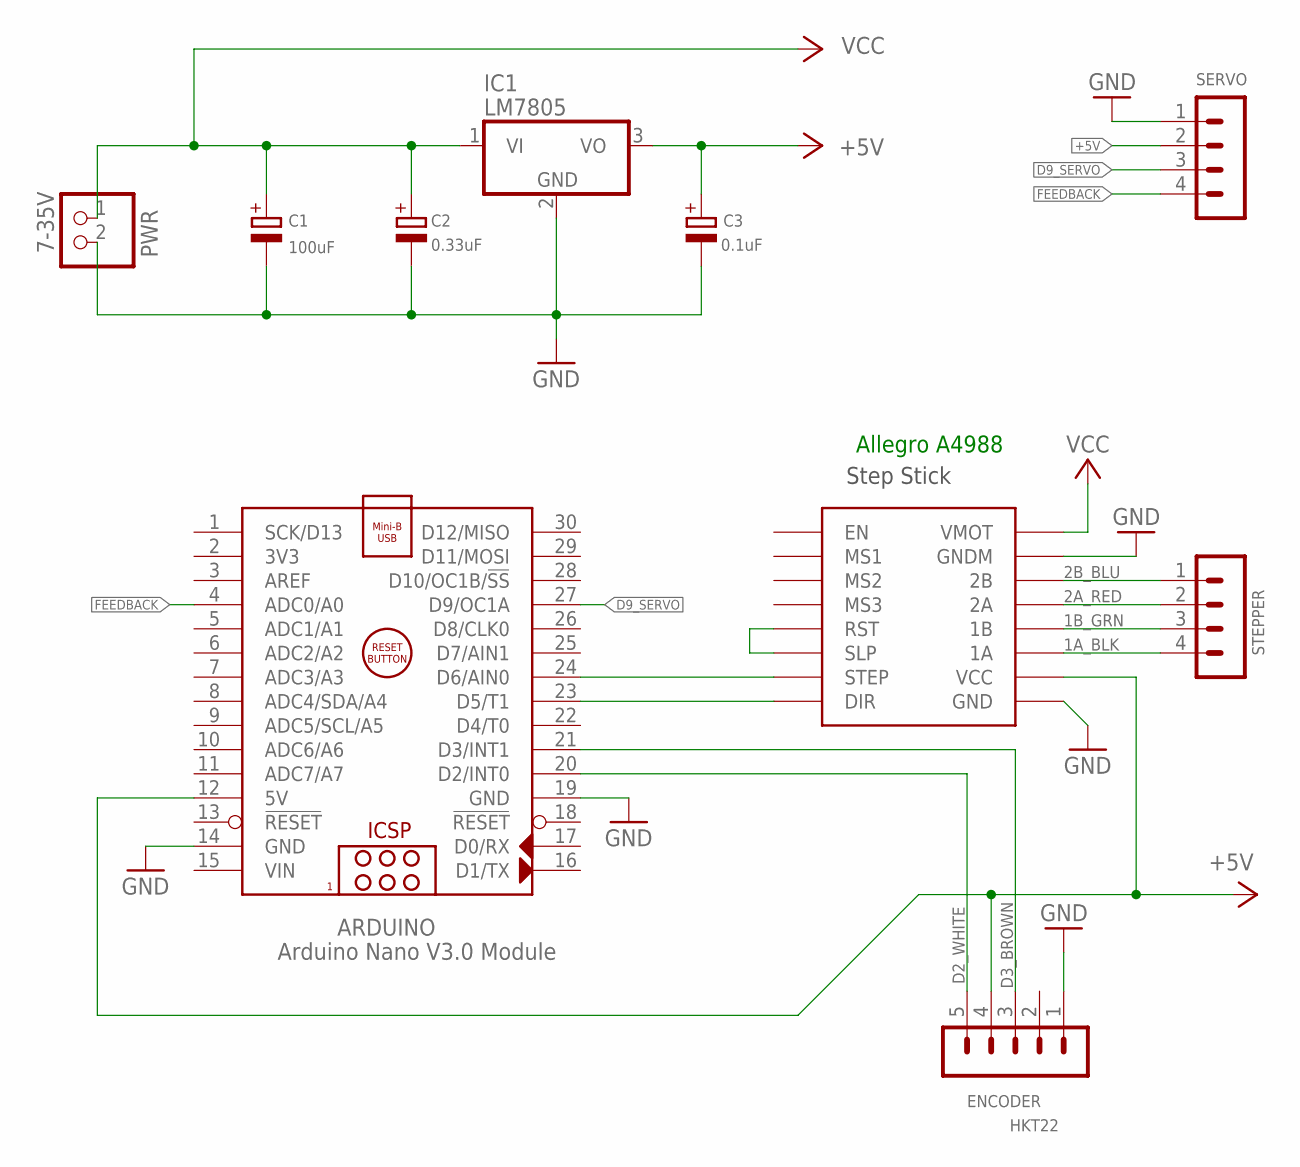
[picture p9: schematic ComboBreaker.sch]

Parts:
ARDUINO: Arduino Nano V3.0 Module; ARDUINO_NANO
C1: 100uF; E2-4
C2: 0.33uF; E2-4
C3: 0.1uF; E2-4
ENCODER: HKT22; MA05-1
IC1: LM7805; TO220V
PWR: 7-35V; JST-PH-2-SMT
SERVO: MA04-1
STEPPER: MA04-1
U$2: Allegro A4988; STEP-STICK

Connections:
1A_BLK: STEPPER.4, U$2.1A
1B_GRN: STEPPER.3, U$2.1B
2A_RED: STEPPER.2, U$2.2A
2B_BLU: STEPPER.1, U$2.2B
+5V: ARDUINO.12 (5V), C3.+, ENCODER.4, IC1.3 (VO), SERVO.2, U$2.VCC
D2_WHITE: ARDUINO.20 (D2/INT0), ENCODER.5
D3_BROWN: ARDUINO.21 (D3/INT1), ENCODER.3
D9_SERVO: ARDUINO.27 (D9/OC1A), SERVO.3
DIR: ARDUINO.23 (D5/T1), U$2.DIR
FEEDBACK: ARDUINO.4 (ADC0/A0), SERVO.4
GND: ARDUINO.14 (GND), ARDUINO.19 (GND), C1.-, C2.-, C3.-, ENCODER.1, IC1.2 (GND), PWR.2 (1), SERVO.1, U$2.GND, U$2.GNDM
RST_SLP: U$2.RST, U$2.SLP
STEP: ARDUINO.24 (D6/AIN0), U$2.SPT (STEP)
VCC: C1.+, C2.+, IC1.1 (VI), PWR.1 (2), U$2.VMOT
VIN: ARDUINO.15 (VIN)

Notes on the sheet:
Allegro A4988

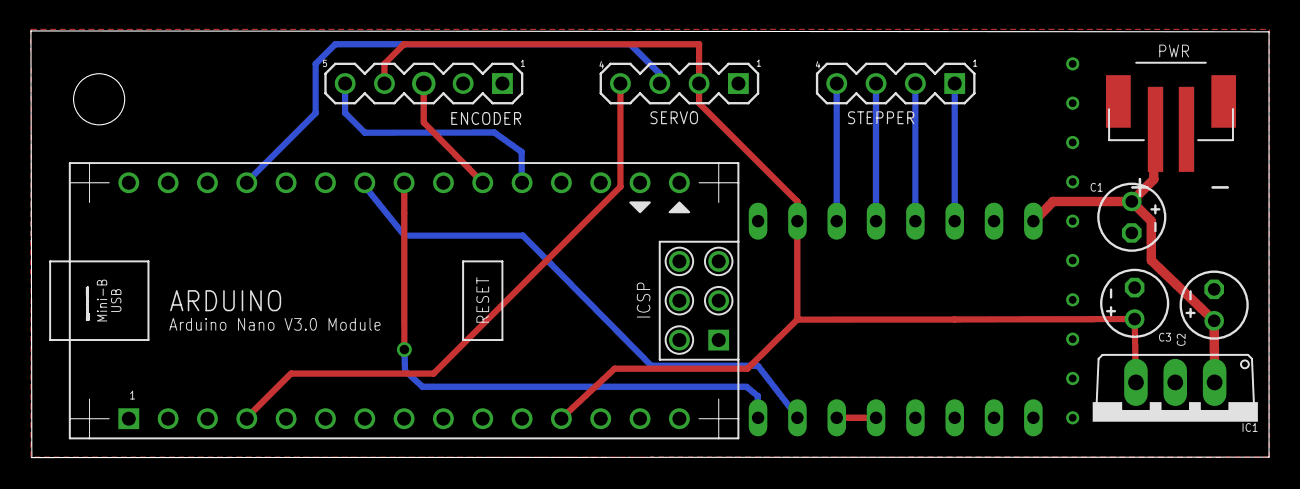
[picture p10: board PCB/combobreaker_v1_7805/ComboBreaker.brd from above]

Board: 2 copper layers, 80.0 x 27.6 mm, 11 parts (0 on the bottom side), 14 nets.

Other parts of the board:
U$3: STAND-OFF

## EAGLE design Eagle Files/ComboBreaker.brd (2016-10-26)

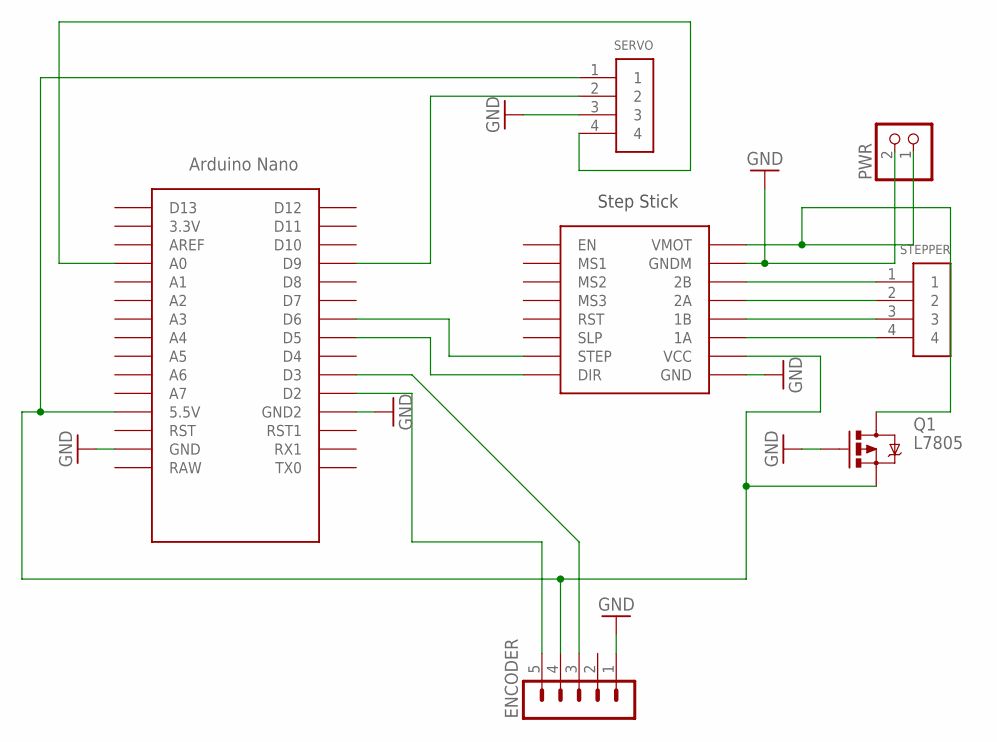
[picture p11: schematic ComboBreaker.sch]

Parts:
ENCODER: MA05-1
PWR: JST_2PIN-SMT; JST-PH-2-SMT
Q1: L7805; TO220V
SERVO: 1X4-BIG; 1X04-BIG
STEPPER: 1X4-BIG; 1X04-BIG
U$1: NANO
U$2: STEP-STICK

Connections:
GND: ENCODER.1, PWR.2 (1), Q1.1 (G), SERVO.3, U$1.GND, U$1.GND1 (GND2), U$2.GND, U$2.GNDM
unnamed: SERVO.2, U$1.D9
unnamed: U$1.D5, U$2.DIR
unnamed: U$1.D6, U$2.SPT (STEP)
unnamed: PWR.1 (2), Q1.2 (D), U$2.VMOT
unnamed: STEPPER.2, U$2.2A
unnamed: STEPPER.1, U$2.2B
unnamed: STEPPER.4, U$2.1A
unnamed: STEPPER.3, U$2.1B
unnamed: SERVO.4, U$1.A0
unnamed: ENCODER.5, U$1.D2
unnamed: ENCODER.4, Q1.3 (S), SERVO.1, U$1.5V (5.5V), U$2.VCC
unnamed: ENCODER.3, U$1.D3

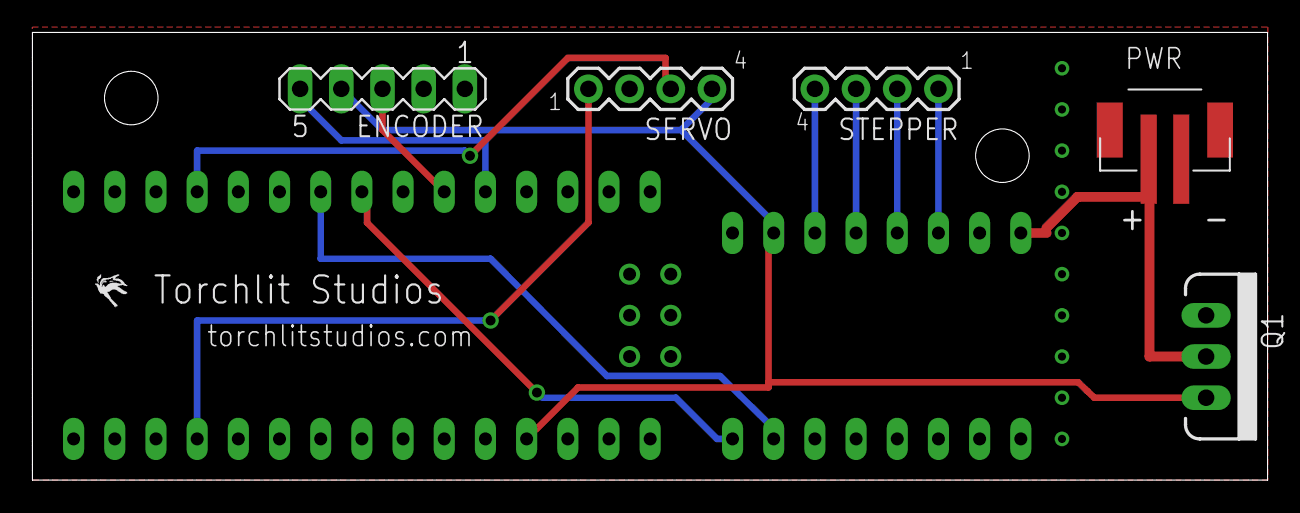
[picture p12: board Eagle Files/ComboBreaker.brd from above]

Board: 2 copper layers, 76.2 x 27.6 mm, 9 parts (0 on the bottom side), 13 nets.

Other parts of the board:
U$3, U$4: STAND-OFF

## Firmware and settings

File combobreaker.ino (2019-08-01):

/*

 C-C-C-C-Combo Breaker
 by samy kamkar
 http://samy.pl/combobreaker
 
 A motorized, battery powered, 3D printed, 
 Arduino-based combination lock cracking device.
 
 current hardware: 
 Stepper Motor (dial): 28STH32-0674B (3.8V 0.67A stepper)
 Rotary Encoder: HKT22-3531 optical rotary encoder (1200steps)
 Servo Motor (shackle): Batan S1213 (with analog feedback)
 Stepper Driver: Allegro A3967 or Allegro A4988 (EasyDriver, 750mA, 1/8th step)
 Microcontroller: Arduino Nano ATmega328P @ 5V
 
 Stepper/Arduino Power: 3S LiPo battery (12V power supply also works)
 Servo Power: L7805 Voltage Regulator
 
 */

// Servo requirements: at least 6.5kg/cm of torque

// TODO: CW could be autodetected by the rotary encoder
// Depending on your stepper wiring, you may need to change CW to true or false
#define CW true // clockwise
#define CCW !CW // counter-clockwise

// Servo details (lifts the shackle)
#include <Servo.h>
#include <Encoder.h>

#define SERVO_DEFAULT 30
#define SERVO_MIN 0
#define SERVO_MAX 200
#define SERVO_PIN 9
#define SERVO_FEEDBACK_PIN A0
#define FB_DIFF 10
#define FB_TOLERANCE 3.5
#define FB_DELAY 500

// Encoder details (pins)
#define ENCODER1 2 // 5
#define ENCODER2 3 // 6
#define ENCODER_STEPS 1200 // 1200 per rotation

// Stepper driver details (controls the dial)
#define DIR_PIN 4
#define STEP_PIN 5

#define STEPS 200
#define MICROSTEPS 8 // was 8 on easydriver

// fastest (us) we can get stepper moving without skipping
// #define MIN_DELAY (1600 / MICROSTEPS) // was 200
#define MIN_DELAY 400

// Number of digits on a Master combo lock
#define DIGITS 40

// C's % is remainder instead of modulo
#define mod(a, b) ((a % b + b) % b)

// For debug
#define BAUDRATE 9600

// this means we can rotate *consistently* 3.125 times per second (187.5rpm):
// 1sec in us / min_delay / (steps * microsteps)
// 1_000_000  / 200       / (200   * 8) = 3.125
int current_digit = 0;

Servo shackle;
Encoder myEnc(ENCODER1, ENCODER2);
//int servo_pos = 0;
long oldPosition;
int mini, maxi, minFeedback, maxFeedback;

void setup() 
{
  Serial.begin(BAUDRATE);

  pinMode(DIR_PIN, OUTPUT);
  pinMode(STEP_PIN, OUTPUT);
  pinMode(SERVO_FEEDBACK_PIN, INPUT);
  shackle.attach(SERVO_PIN); 
  oldPosition = myEnc.read();

  calibrateServo();
}

void loop()
{
  brute(-1, -1, -1);

  for (int i = 0; i < ceil(DIGITS/3); i++)
  {
    // turn to new position
    spinto(0, i * 3, CCW);

    // hold shackle high to find left and right
    shackleHigh();
    spinto(0, (i-1)*3, CW);
    //    delay(100);

    Serial.print("spin low ");
    Serial.print(oldPosition);
    Serial.print(" ");
    spinto(0, (i+1)*3, CCW);
    //    delay(100);
    Serial.print(oldPosition);
    Serial.println("");

    //    delay(100);
    spinto(0, i * 3, CCW);

    shackleMid();
    delay(2000);
  }

  //  spinto(1, 0, CW);
  //  brute(16, -1, 16);
  //  pin(0, 0, 0);
  //  openShackle();
}

// pulls the shackle up
// NOTE: if you do this, you should immediately
// detect if the servo actually moved up, and if not,
// return back to shackleMid(), otherwise you'll be
// putting stress on the motor and 3d printed case
void shackleHigh()
{
  shackle.write(maxi + (FB_DIFF*(FB_TOLERANCE-1)));
}

// puts the shackle in middle position
void shackleMid()
{
  shackle.write(maxi);
}

// attempts to open the shackle *safely*
boolean openShackle()
{
  int fb;
  boolean ret = false;

  shackle.write(maxi + (FB_DIFF*FB_TOLERANCE*1.5));
  delay(300);

  fb = analogRead(SERVO_FEEDBACK_PIN);
  if (fb - maxFeedback > FB_DIFF*FB_TOLERANCE)
  {
    Serial.println("OPENED!");
    ret = true;
  }
  else
  {
    ret = false;
    Serial.println("not opened :(");
  }

  shackleMid();
  return ret;
}

// detect the middle and high positions of the servo
void calibrateServo()
{
  int fb;
  int i = SERVO_DEFAULT;

  shackle.write(i);
  delay(500);
  fb = analogRead(SERVO_FEEDBACK_PIN);

  Serial.println(fb);
  for (i -= FB_DIFF; i > SERVO_MIN; i -= FB_DIFF)
  {
    Serial.print("i=");
    Serial.print(i);
    shackle.write(i);
    mini = i;
    delay(FB_DELAY);
    minFeedback = analogRead(SERVO_FEEDBACK_PIN);
    Serial.print(" fb=");
    Serial.println(minFeedback);

    // if difference is less than 10, we can't move!
    if (fb - minFeedback < FB_DIFF)
    {
      mini = i + (FB_DIFF*FB_TOLERANCE);
      Serial.println("crap!");
      break;
    }
    fb = minFeedback;

  }


  for (i+=FB_DIFF*2; i <= SERVO_MAX; i += FB_DIFF)
  {
    Serial.print("i=");
    Serial.print(i);
    shackle.write(i);
    maxi = i;
    delay(FB_DELAY);
    maxFeedback = analogRead(SERVO_FEEDBACK_PIN);
    Serial.print(" fb=");
    Serial.println(maxFeedback);

    // if difference is less than 10, we can't move!
    if (maxFeedback - fb < FB_DIFF)
    {
      maxi = i - (FB_DIFF*FB_TOLERANCE);
      Serial.print("crap!! changing to ");
      Serial.println(maxi);
      shackleMid();
      break;
    }
    fb = maxFeedback;

  }

  Serial.print("mini=");
  Serial.print(mini);
  Serial.print(" maxi=");
  Serial.print(maxi);
  Serial.println("");
}

// brute force pin numbers based off of the
// mathematical congruencies of the lock
void brute(int pin1, int pin2, int pin3)
{
  int si = pin1, sj = pin2, sk = pin3;

  if (pin1 == -1)
    si = pin2 >= 0 ?
    (pin2 + 2) % 4 :
    pin3 >= 0 ?
    pin3 % 4 : 0;

  if (pin2 == -1)
    sj = pin1 >= 0 ?
    (pin1 + 2) % 4 :
    pin3 >= 0 ?
    (pin3 + 2) % 4 : 0;

  if (pin3 == -1)
    sk = pin1 >= 0 ?
    pin1 % 4 :
    pin2 >= 0 ?
    (pin2 + 2) % 4 : 0;

  Serial.println(si);
  Serial.println(sj);
  Serial.println(sk);
  Serial.println("go");

  for     (int i = si; (pin1 == i || pin1 == -1) && i < DIGITS; i += 4)
    for   (int j = sj; (pin2 == j || pin2 == -1) && j < DIGITS; j += 4)
      for (int k = sk; (pin3 == k || pin3 == -1) && k < DIGITS; k += 4)
      {
        Serial.print("testing: ");
        Serial.print(i);
        Serial.print(" ");
        Serial.print(j);
        Serial.print(" ");
        Serial.print(k);
        Serial.println();

        pin(i, j, k);
        if (openShackle())
          return;

        delay(100);
      }

}

// enter a full combination through the dial
void pin(int pin1, int pin2, int pin3)
{
  // clockwise 3 times, then to first number  
  spinto(3, pin1, CW);

  // counterclockwise once, then to second
  spinto(1, pin2, CCW);

  // clockwise to third number
  spinto(0, pin3, CW);
}

// spin to a specific digit,
// possibly with some additional rotations
void spinto(int spins, int digit, boolean cw)
{
  digitalWrite(DIR_PIN, cw ? HIGH : LOW);

  // spin some amount all the way?
  for (int i = 0; i < spins; i++)
  {
    step(STEPS);
//    delay(1000);
  }

  // track where we are for next time (get set later)
  int tmp = digit;
  Serial.print("going to ");
  Serial.print(digit);
  Serial.print(" cur=");
  Serial.print(current_digit);

  if (cw == CW)
    digit = (DIGITS - digit) + current_digit;
  else
    digit = digit - current_digit;

  digit = mod(digit, DIGITS);

  // track where we are for next time
  current_digit = tmp;

  Serial.print(" moving ");
  Serial.println(digit);
  step(digit * (STEPS / DIGITS));
//  delay(1000);
}

/*
void rotate(int digits, boolean cw)
 {
 rotate(0, digits, cw);
 }
 
 void rotate(int spins, int digits, boolean cw)
 {
 digitalWrite(DIR_PIN, cw ? HIGH : LOW);
 
 // spin some amount all the way?
 for (int i = 0; i < spins; i++)
 {
 step(STEPS);
// delay(1000);
 }
 
 
 step(digits * (STEPS / DIGITS));
// delay(1000);
 }
 */

// step to location
// TODO: return encoder feedback
void step(int steps)
{
  long newPosition;
  for (int i = 0; i < steps * MICROSTEPS; i++)
  {
    digitalWrite(STEP_PIN, LOW);
    delayMicroseconds(MIN_DELAY);
    digitalWrite(STEP_PIN, HIGH);
    delayMicroseconds(MIN_DELAY);
  }

  // get encoder position
  newPosition = myEnc.read();
  if (newPosition != oldPosition)
  {
    //      oldPosition = newPosition;
    oldPosition = mod(newPosition, ENCODER_STEPS);//XXX
    Serial.print("newpos=");
    Serial.print(newPosition);
    Serial.print(" actual=");
    Serial.print((int)(oldPosition / DIGITS));
    Serial.print(" pos=");
    Serial.println(oldPosition);
  }
}

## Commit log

2015-05-14 Added code + 3d models
    [combo-breaker-chassis.igs, pancake-stepper-gripper.igs, stepper-long-gripper.igs]
2015-05-17 added f3d (fusion 360 archive file) for the chassis
    [combo-breaker-chassis.f3d]
2015-05-17 added f3d (fusion 360 archive file) for pancake stepper gripper
    [pancake-stepper-gripper.f3d]
2015-08-03 Initial Commit
    Still requires verification and testing. Do not build until tested!
    [ComboBreaker.brd, ComboBreaker.sch]
2015-08-03 Finished Design
    Added Encoder header and verified design against documentation.
    releasing for first piece prototype. please report any errors.
2015-08-04 prettied up
    prettied things up and added some pictures and BOM
    [Combo Breaker BOM.xlsx, ComboBreaker.brd]
2015-08-04 Added Standoff Holes
    #4 Philips standoff holes added to board
2015-08-04 added stl files
    stl files added for 3d printing
    [combo-breaker-chassis.stl, pancake-stepper-gripper.stl, stepper-long-gripper.stl]
2017-03-15 PCB with OKI-78SR
    * Corrected pinouts for LM7805
    * Replaced LM7805 with OKI-78SR switching regulator. This is a “No heat
    sink” direct replacement for 3-terminal 78xx-series linear regulators.
    * Added 100uf decoupling capacitor
    * Updated Arduino Nano device/footprint
    * Updated A4988 StepStep device/footprint
    * Added 4-pin header for OLED display
    * Added trace between RST and SLP on A4988
    * Redesigned PCB layout
    [ComboBreaker.brd, ComboBreaker.sch]
2017-03-15 PCB with LM7805
    * Added decoupling capacitor
    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
    [ComboBreaker.brd, ComboBreaker.sch]
2017-03-15 PCB with OKI-78SR
    *** Converted EAGLE files to kicad ***
    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
    [ComboBreaker.kicad_pcb, ComboBreaker.sch]
2017-03-16 Added I2C OLED Display
    * Added I2C header pins for OLED display
    * Reoriented JST power connector
    * Rerouted VCC
    [ComboBreaker.brd, ComboBreaker.sch]
2017-03-19 Updated v2 Eagle PCB layout
    * Added standoff holes
    * Added descriptions
    * Added mitre to board corners
    [ComboBreaker.brd, ComboBreaker.sch]
2017-03-19 Updated PCB
    * Moved silkscreen text to tPlace layer
    * Moved holes in Arduino Nano module to Reference layer
    [ComboBreaker.brd, ComboBreaker.sch]
2017-03-20 Updated v2 Eagle PCB
    * Added more silkscreen details
    * Minor adjustments to footprints
    TO-DO:
    * Confirm pinout wire colors
    [ComboBreaker.brd, ComboBreaker.sch]
2017-03-20 Updated v2 Eagle PCB (Prototype Ordered!)
    This is final prototype design sent to printers!
    * Added Master Lock logo
    * Added pinout wire colors to bottom silkscreen
    * Added pin identifiers to servo/stepper/encoder pins on top silkscreen
    * Redraw ground pour polygons
    [ComboBreaker.brd, ComboBreaker.sch]
2017-03-31 Update v2 Eagle PCB
    * Fix drill hole size on header pin package
    [ComboBreaker.brd, ComboBreaker.sch]
2017-04-05 Updated v2 Eagle PCB
    * Renamed Stepper pinout labels
    * Added ground connections
    * Manually set MIN_DELAY
    [ComboBreaker.brd, ComboBreaker.sch]
2017-05-08 Updated ComboBreaker.ino code
    * Corrected DIR and STEP pins
    * Added delayMicroseconds(MIN_DELAY); to line 362 which resolved the
    issue with the stepper motor not stepping correctly
    [ComboBreaker.brd, ComboBreaker.sch]
2017-09-25 Added GND pour to TOP layer
    *** Added GND pour to TOP layer to resolve issues with SMD JST connector etc.
    *** Adjusted JST connector pin name to GND.
    [ComboBreaker.brd, ComboBreaker.sch]
2017-09-25 Minor changes to schematic
    [ComboBreaker.brd, ComboBreaker.sch]
2017-09-28 Updated header pins to circles from ovals
    [ComboBreaker.brd, ComboBreaker.sch]
2017-10-05 Updated drill size to .35
    * Updated drill sizes on most holes to .35
    * Adjusted Mini-B USB connector outline on Arduino Nano silkscreen
    [ComboBreaker.brd, ComboBreaker.sch]
2017-10-06 v3 PCB
    Minor changes
    V3 send to fabrication
    [ComboBreaker.brd, ComboBreaker.sch]

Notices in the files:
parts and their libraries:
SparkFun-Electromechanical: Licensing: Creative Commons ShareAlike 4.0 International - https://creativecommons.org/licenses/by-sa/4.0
